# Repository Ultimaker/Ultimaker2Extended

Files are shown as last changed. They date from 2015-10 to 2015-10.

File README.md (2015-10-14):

# Ultimaker2Extended
Bill of Materials and parts for Ultimaker2Extended

In this repository you will find the documentation and source files for all parts in the Ultimaker2 Extended 3D printer. In the Bill Of Materials (BOM) repository all the parts are numbered and named with the correct amounts. Every part has a separate directory containing all the relevant files. The 9407 is a subsytem. The parts can also be found in the separate directories.

The electronic files can be found in the directory 1155 Print Table Heated Bed; 1249 Ulticontroller board and 1546 Ultimainboard V2.1.4.

If you are missing a part or information feel free to file an issue on github.

Harma Woldhuis <br>
Ultimaker Research and Development

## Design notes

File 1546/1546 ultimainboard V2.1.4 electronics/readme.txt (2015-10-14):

The UltiMainboard 2.x.x electronics are released under GPLv2 license.
And are based on the origonal Ultimaker electronics design by Jan-Jaap Schuurman, Siert Wijnia and ErikDeBruijn at http://reprap.org/wiki/Ultimaker's_v1.5.7_PCB
As well as the ArduinoMega2560 by Arduino: http://arduino.cc/en/Main/arduinoBoardMega2560

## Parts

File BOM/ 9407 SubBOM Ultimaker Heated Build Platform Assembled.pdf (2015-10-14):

## SubBOM

Total quantity parts | 40
Partnummer | Naam | Quantity
1152 B | Table Spring D2150 | 3
1153 B | Print Table Base Plate | 1
1155 C | Print Table Heated Bed | 1
1170 B | Square Flanged Linear Bearing LMK12LUU | 2
1183 C | Heated Bed Cable | 1
1187 A | Trapezoidal Lead Nut | 1
1202 B | ISO 7380 M3x10 | 6
1206 B | ISO 7380 M3x20 | 1
1217 A | ISO 7380 M4x10 A2 | 8
1243 B | Heated Bed Cable Clip | 1
1256 A | Build Platform Glass Retainer Back | 2
1257 B | Knurled Nut Platform | 3
1288 A | Washer M6 | 3
1355 B | Heated Bed Bolt 8 mm | 4
1356 B | Heated Bed Bolt 20 mm | 3

## 9407 Ultimaker Heated Build Platform Assembled

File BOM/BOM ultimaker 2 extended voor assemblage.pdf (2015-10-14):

9068-A | Ultimaker 2 Extended voor assemblage

per 30-12-2014
Total quantity parts | 318
Partnummer | | Name | Quantity
1011 | B | Y-linear shaft | 2
1012 | B | X-linear shaft | 2
1021 | A | Ball Bearing 688-2RS | 1
1024 | D | Limit Switch, Black Short Wire | 1
1056 | A | Sintered Bushing | 4
1065 | B | Linear Bearing LM6LUU | 2
1069 | A | Tube Coupling Collet | 2
1071 | A | Clamp Clip | 2
1140 | A | Feeder Spring DR2110 | 1
1156 | A | Z-shaft Cap Bottom | 2
1165 | A | Timing Pulley 5mm Shaft GT2 | 2
1166 | C | Timing Pulley 8mm Shaft GT2 | 8
1167 | D | Timing Pulley Double 8mm Shaft GT2 | 1
1168 | B | Sliding Block Spring | 4
1171 | B | Double flat Cable 10 Wire | 1
1172 | A | Print Head Shaft X | 1
1173 | A | Print Head Shaft Y | 1
1176 | A | Spacer 8.2x10x5 | 2
1177 | A | Spacer 8.2x10x10 | 4
1178 | A | Spacer 8.2x10x25 | 1
1179 | D | Feeder Motor | 1
1186 | E | Print Head Cable | 1
1188 | A | Timing Belt GT2 200 | 2
1189 | A | Timing Belt GT2 610 | 4
| | nuts and bolts
1200 | A | ISO 7380 M3x8 | 8
1201 | C | Washer Large M3 | 12
1202 | B | ISO 7380 M3x10 | 7
1203 | B | ISO 7380 M3x12 | 11
1204 | B | ISO 7380 M3x16 | 44
1206 | B | ISO 7380 M3x20 | 1
1207 | B | ISO 7380 M3x25 | 16
1209 | C | Nut M3 | 1
1211 | A | Set Screw M4x4 | 11
1212 | B | Set Screw M3x3 | 1
1213 | B | DIN 562 Square Nut M3 A2 | 40
1214 | A | ISO 7040 Nut M3 Prev. torque A2 | 12
1220 | A | Ball Bearing F688-2RS | 8
1234 | E | Bottom Panel UM2 | 1
1235 | D | Top Panel UM2 | 1
1240 | C | Main Board Electronics Cover | 1
1241 | B | Motor Spacer UM2 | 2

1242 | A | Spacer 3.2 x 6x 10 | 4
1244 | A | Knob Front UM2 | 1
1245 | A | Knob Housing UM2 | 1
1247 | A | Display Oled Blue | 1
1249 | A | Ulticontroller Board | 1
1250 | B | SD card 4G | 1
1251 | B | Ulticontroller Electronics Cover | 1
1255 | A | Sliding Block Half UM2 | 8
1258 | G | Feeder Part A | 1
1259 | G | Feeder Part B | 1
1264 | D | Feeder Nut Holder | 1
1266 | C | Bowden tube | 1
1268 | B | Heater Cartridge 24V 25W | 1
1279 | A | Feeder Ring | 1
1281 | C | Braided Sleeve Clip | 5
1287 | A | Washer M7 | 1
1301 | D

Integrated nozzle heater block
3mm filament | 1
1306 | C | Hot end holder bottom | 1
1307 | C | Hot end holder top | 1
1308 | C | Cooling Rib Hot End | 1
1310 | B | Hot end Isolator | 1
1311 | A | Spring D2000 | 1
1313 | A | Model Cooling Fan 12VDC 0.1 A | 2
1315 | A | Jumper | 2
1321 | C | Print Head Middle | 1
1322 | D | Print Head Bottom | 1
1330 | B | Hot-end Cooling Fan 5VDC 0.08A | 1
1348 | A | ISO 7380 M3x4 A2 | 4
1351 | A | ISO 4762 M2,5x10 | 2
1354 | A | ISO 724 Hex nut M7 | 1
1357 | A | DIN 913 M3x14 | 1
1358 | A | chipboard panel screw 2.5x16 | 8
1363 | A | Ferrite Core | 2
1364 | A | PTFE Isolator Coupler Glass Filled 3.2 mm | 1
1365 | A | Dual Fan Bracket Safety | 1
1366 | A | PTFE nozzle ring | 1
1521 | A | Short Print Head Thumb Screw | 4
1546 | A | Ultimainboard V2.1.4 | 1
1748 | D | Print head top single hole | 1
1814 | | feeder knurled wheel long | 1

1816 | feeder idler lever part A | 1
1817 | feeder idler lever part B | 1
2201 | E | Z-linear shaft | 2
2202 | A | Z-Motor with Trapezoidal Lead Screw | 1
2203 | B | X,Y motor | 2
2204 | B | Limit Switch, Blue Wire | 1
2205 | B | Limit Switch, Red Wire | 1
2206 | A | LED Strip Cold white | 1
2211 | B | Back Panel | 1
2212 | A | Left Panel | 1
2213 | A | Right Panel | 1
2214 | A | Front Panel | 1
2215 | A | Print Table Back Cover | 1
2222 | A | Cable Cover | 2
2225 | C | PT100B sensor | 1

9407

subBOM Ultimaker Heated Build
Platform Assembled | 1

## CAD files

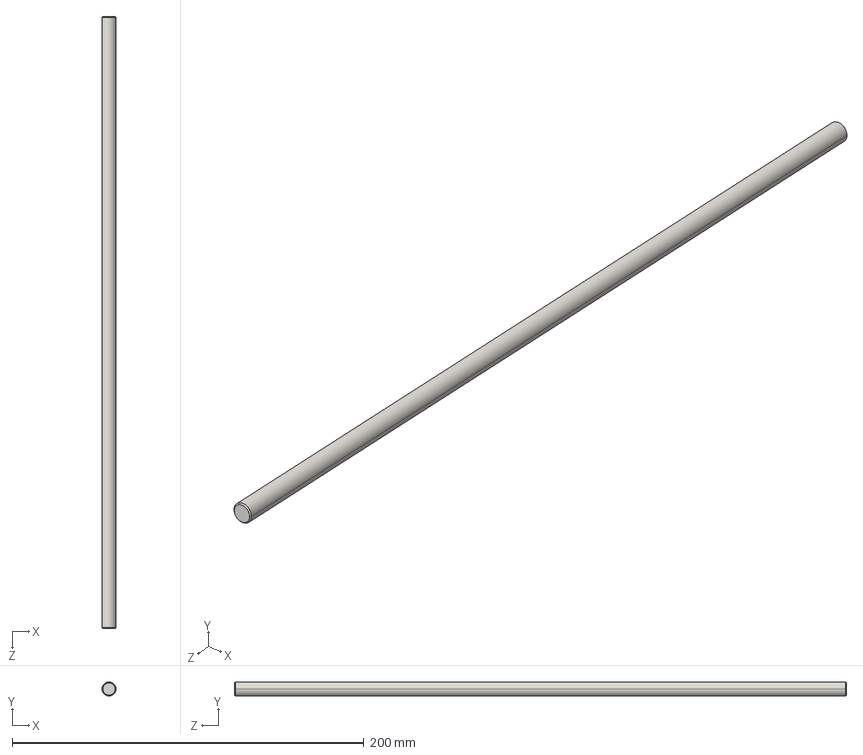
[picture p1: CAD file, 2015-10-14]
1011/1011-B.STEP
8.00 x 8.00 x 348.0 mm

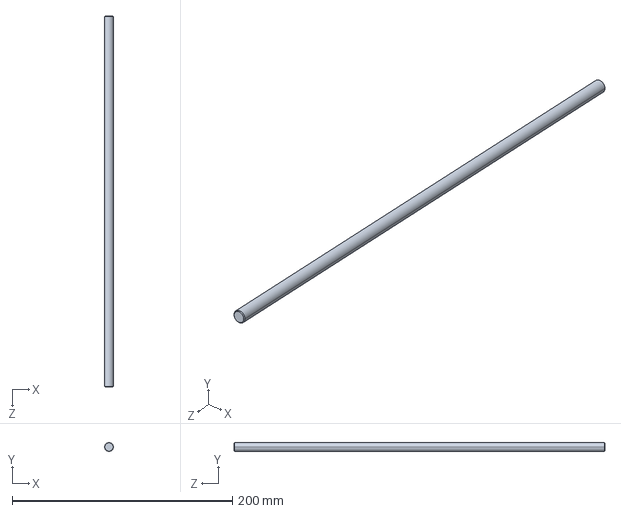
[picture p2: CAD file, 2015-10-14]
1012/1012-B.STEP
8.00 x 8.00 x 337.0 mm

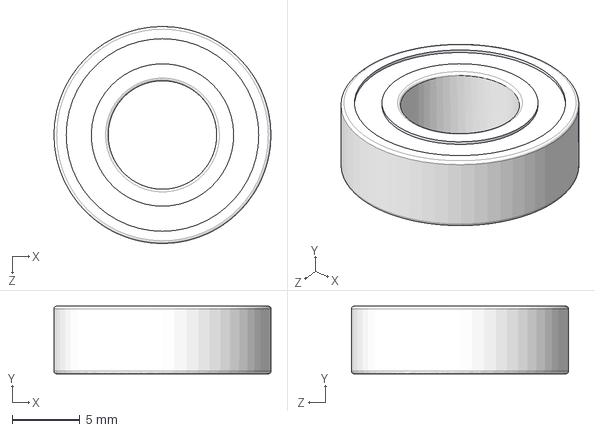
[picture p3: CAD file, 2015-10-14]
1021/1021-Z1P-A.STEP
16.0 x 5.00 x 16.0 mm

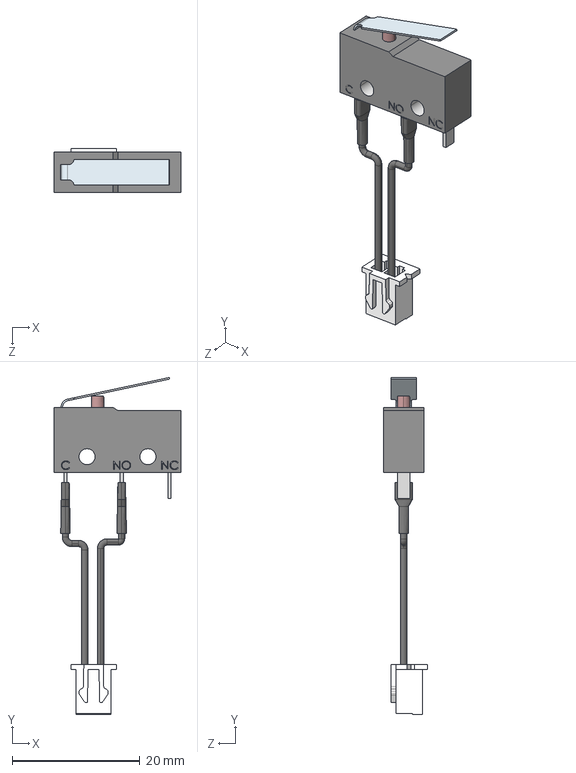
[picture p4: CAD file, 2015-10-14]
1024/1024-D.STEP
19.8 x 52.7 x 6.90 mm

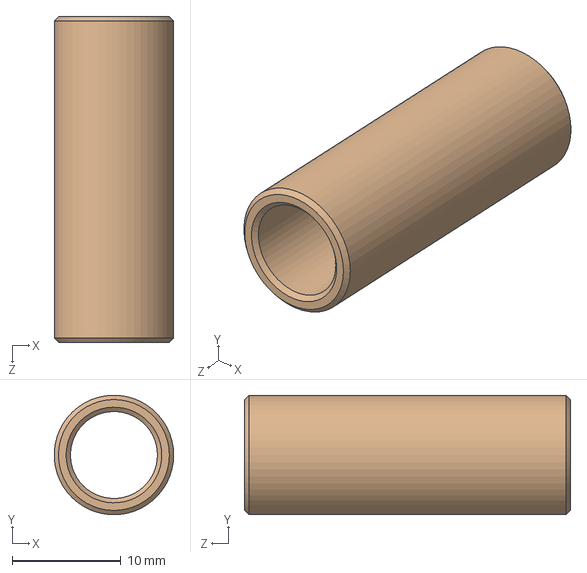
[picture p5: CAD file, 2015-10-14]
1056/1056-A2P-A.STEP
11.0 x 11.0 x 30.0 mm

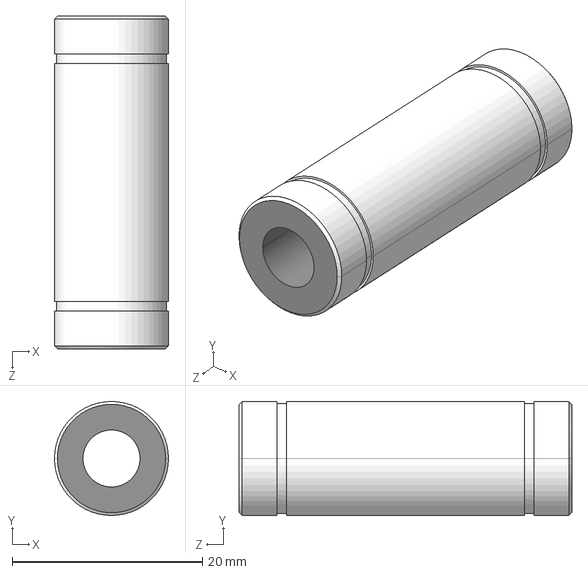
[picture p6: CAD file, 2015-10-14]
1065/1065-Z1P-B.STEP
12.0 x 12.0 x 35.0 mm

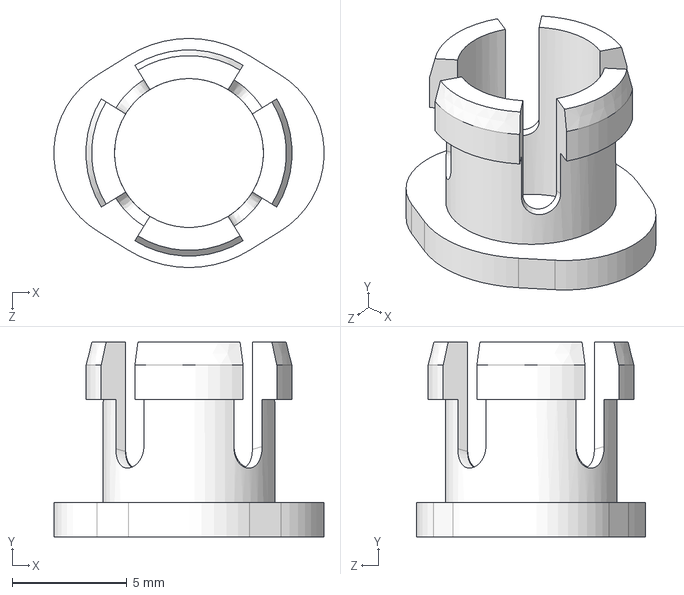
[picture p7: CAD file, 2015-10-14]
1069/1069-Z1P-A.STEP
11.8 x 8.50 x 10.00 mm

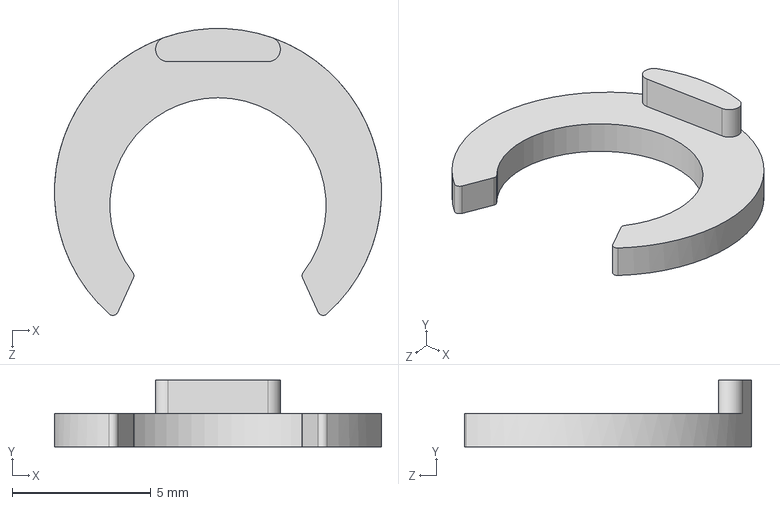
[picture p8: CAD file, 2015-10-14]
1071/1071-Z1P-A.STEP
11.8 x 2.40 x 10.3 mm

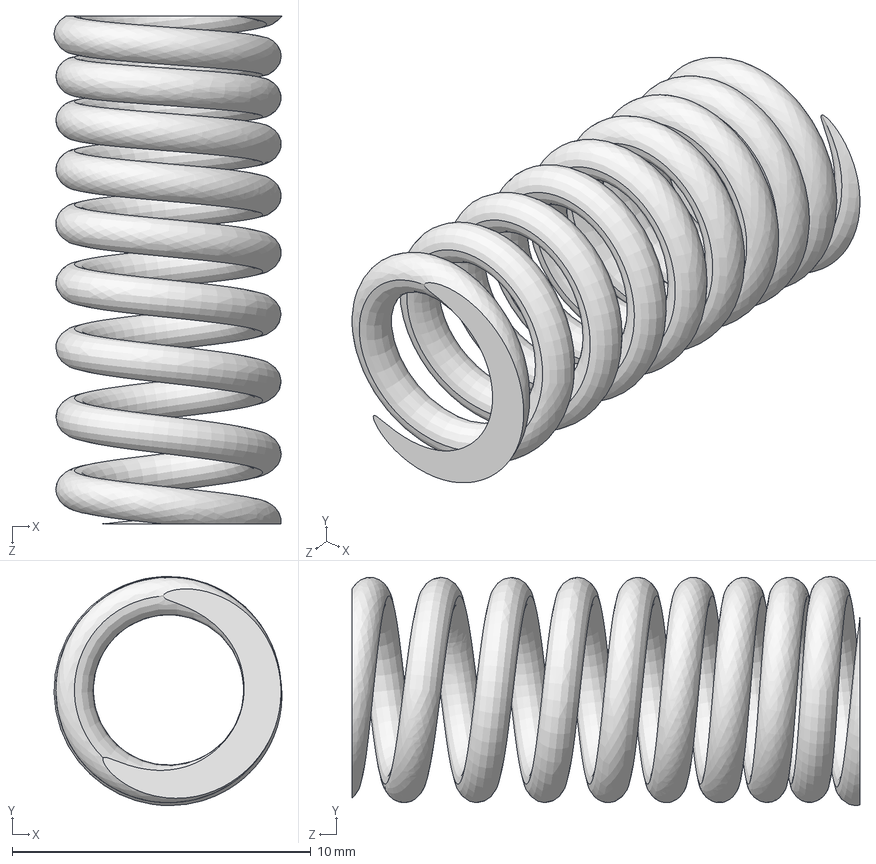
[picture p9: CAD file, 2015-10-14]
1140/1140-01.STEP
7.63 x 7.67 x 17.0 mm

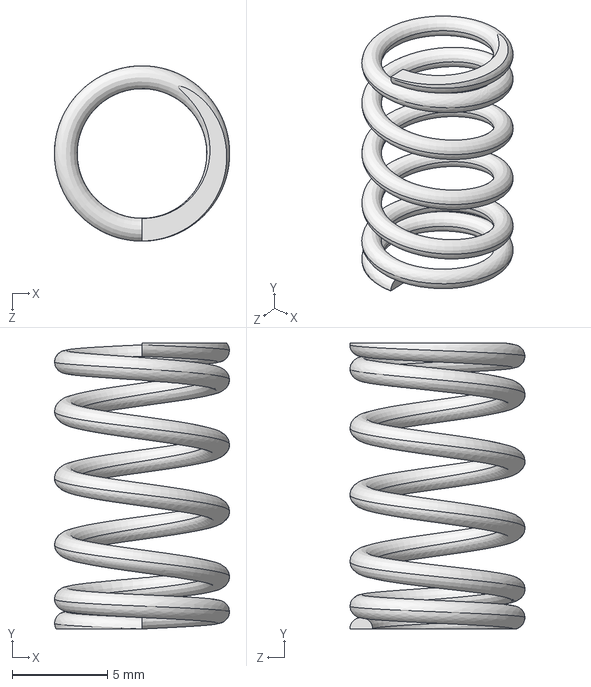
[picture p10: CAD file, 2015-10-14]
1152/1152-B2P-B.STEP
9.20 x 15.0 x 9.20 mm

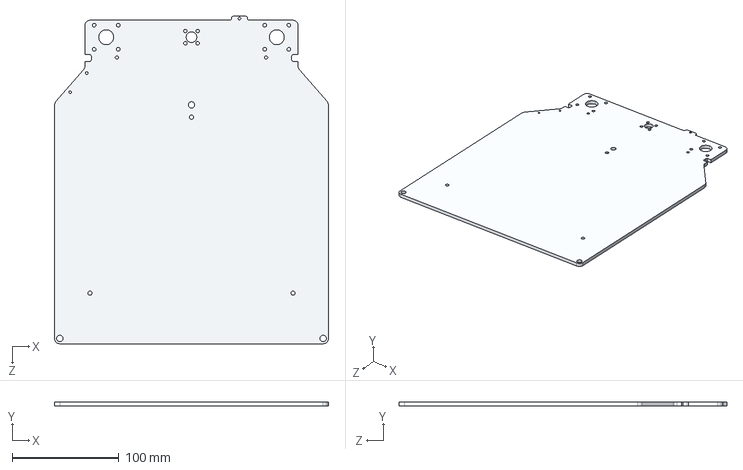
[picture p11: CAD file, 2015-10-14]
1153/1153-B2P-B.STEP
257.0 x 4.00 x 307.2 mm

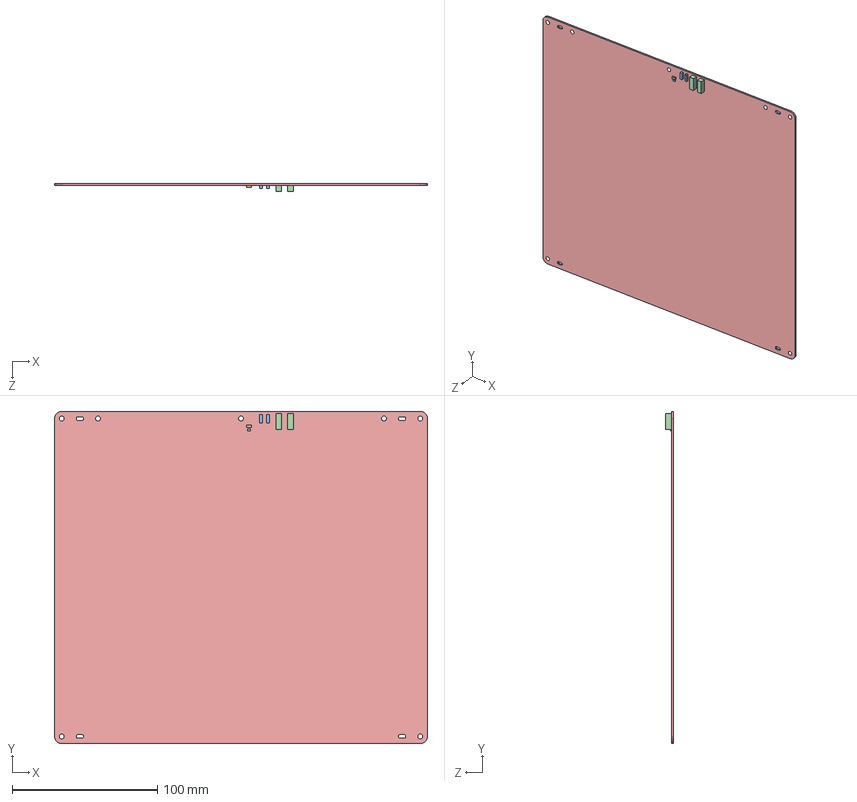
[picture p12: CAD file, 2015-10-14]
1155/1155-C.STEP
257.0 x 229.0 x 5.50 mm

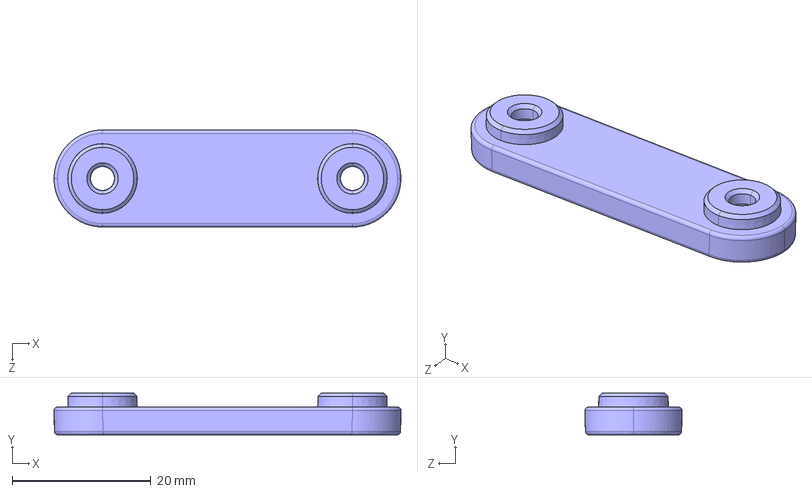
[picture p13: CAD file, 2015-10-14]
1156/1156-B2P-A.STEP
50.0 x 6.00 x 14.0 mm

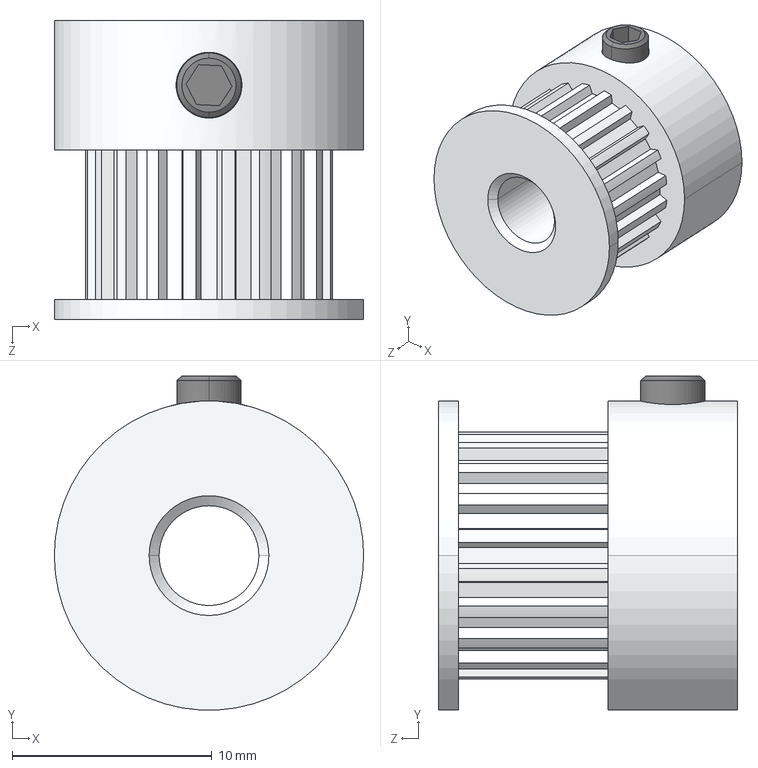
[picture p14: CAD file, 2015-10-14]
1165/1165-B2P-A.STEP
15.5 x 16.7 x 15.0 mm

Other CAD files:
1166/1166-C.STEP
1167/1167-D.STEP
1168/1168-B2P-B.STEP
1170/1170-B2P-B.STEP
1172/1172-B2P-A.STEP
1173/1173-B2P-A.STEP
1176/1176-B1P-A.STEP
1177/1177-B1P-A.STEP
1178/1178-B1P-A.STEP
1179/1179-D.STEP
1187/1187-B2P-A.STEP
1188/1188-B2P-A.STEP
1189/1189-B2P-A.STEP
1200/1200-Z1P-A ISO 7380 M3x8 new.STEP
1201/1201-Z1P-C.STEP
1202/1202-Z1P-B.STEP
1203/1203-Z1P-B.STEP
1204/1204-Z1P-B.STEP
1206/1206-Z1P-B.STEP
1207/1207-Z1P-B.STEP
1209/1209-C.STEP
1211/1211-Z1P-A.STEP
1212/1212-Z1P-B.STEP
1213/1213-Z1P-B.STEP
1214/1214-Z1P-A.STEP
1217/1217-A.STEP
1220/1220-A.STEP
1234/1234-B2P-E Buitenkant.DXF
1235/1235-B2P-D Buitenkant.DXF
1235/1235-B2P-D.STEP
1240/1240-C.DXF
1240/1240-C.STEP
1241/1241-B2P-B.STEP
1242/1242-B2P-A.STEP
1243/1243-B2P-B.STEP
1244/1244-B2P-A.STEP
1245/1245-B2P-A.STEP
1247/1247-B2P-A.STEP
1250/1250-B.STEP
1251/1251-B.DXF
1255/1255-B2P-A.STEP
1256/1256-B2P-A.STEP
1257/1257-B2P-B.STEP
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

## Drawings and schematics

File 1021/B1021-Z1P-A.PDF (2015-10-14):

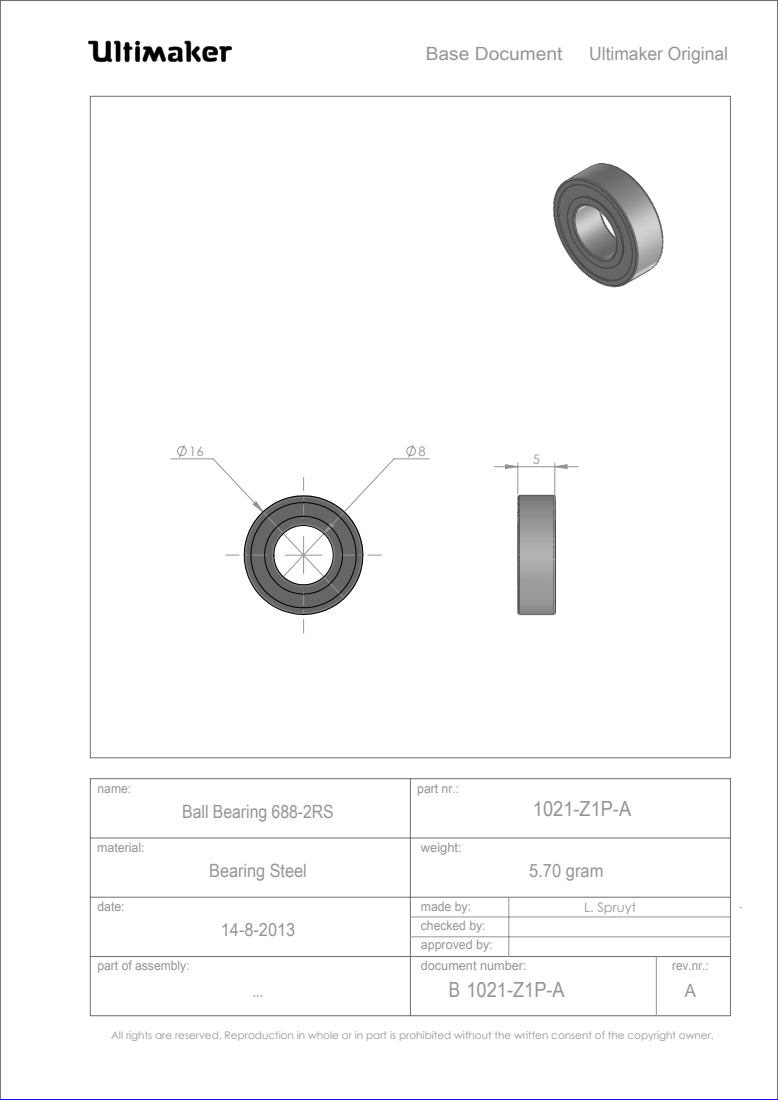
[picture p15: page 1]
Bearing Steel; 5.70 gram; Ball Bearing 688-2RS; Ultimaker Original; part of assembly:; rev.nr.:; part nr.:; made by:; Base Document; approved by:; checked by:; L. Spruyt; document number: B 1021-Z1P-A

All rights are reserved. Reproduction in whole or in part is prohibited without the written consent of the copyright owner.

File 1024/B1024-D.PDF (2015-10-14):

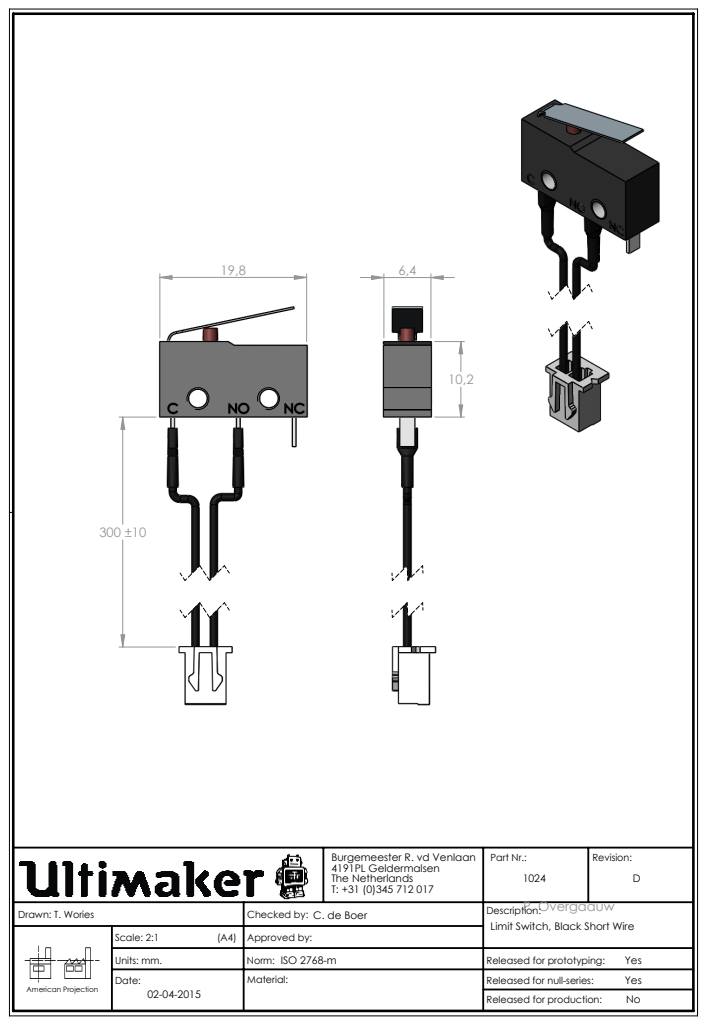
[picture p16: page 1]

Burgemeester R. vd Venlaan 4191PL Geldermalsen The Netherlands T: +31 (0)345 712 017 | Part Nr.: 1024 | Revision: D

Drawn: T. Wories | Checked by: C. de Boer | P. Overgaauw Description: Limit Switch, Black Short Wire

American Projection | Scale: 2:1 (A4) | Approved by:

Units: mm. | Norm: ISO 2768-m | Released for prototyping: Yes
Date: 02-04-2015 | Material: | Released for null-series: Yes

Released for production:

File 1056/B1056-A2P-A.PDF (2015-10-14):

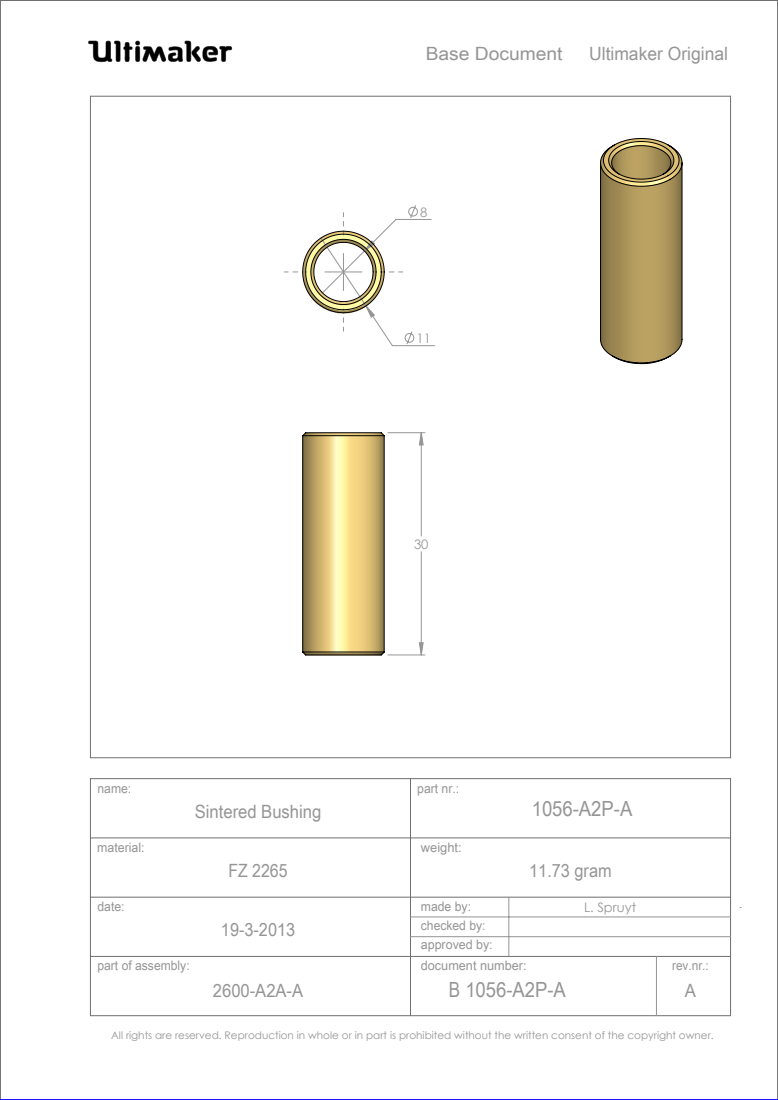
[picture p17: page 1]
11.73 gram; Sintered Bushing; Ultimaker Original; part of assembly:; rev.nr.:; part nr.:; made by:; Base Document; approved by:; checked by:; L. Spruyt; document number: B 1056-A2P-A

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

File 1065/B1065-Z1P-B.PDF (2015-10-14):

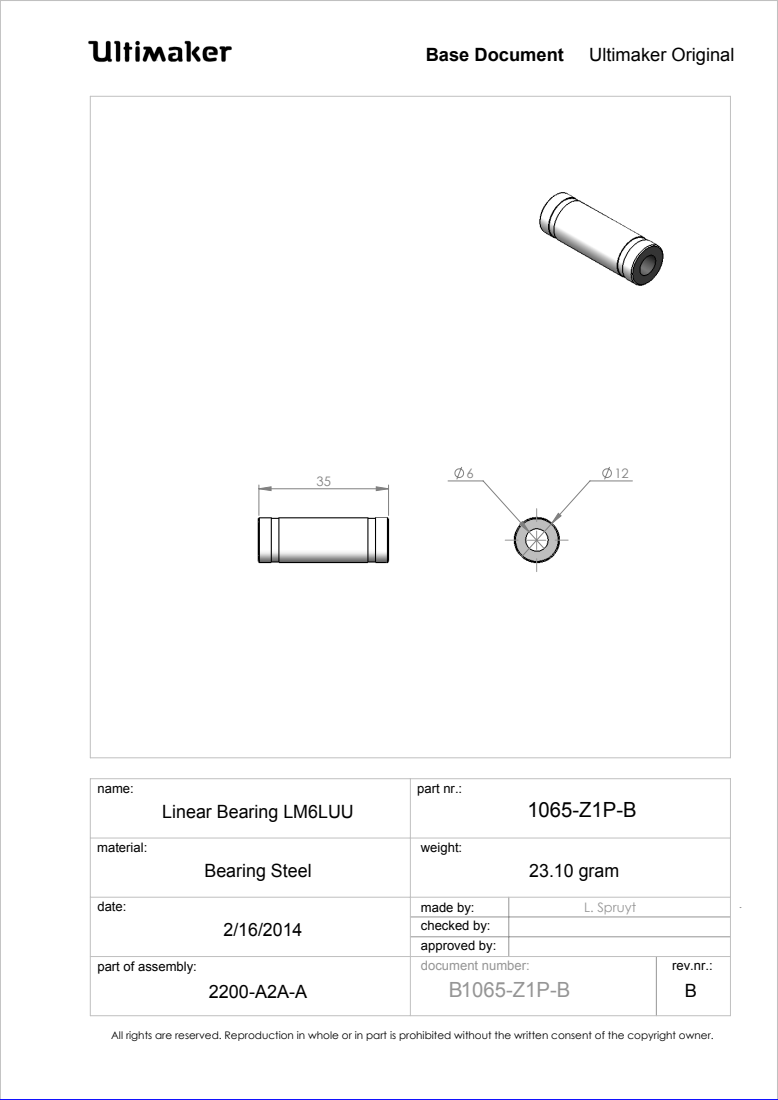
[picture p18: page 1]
Bearing Steel; 23.10 gram; Linear Bearing LM6LUU; Ultimaker Original; part of assembly:; rev.nr.:; part nr.:; made by:; Base Document; approved by:; checked by:; L. Spruyt; document number:

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

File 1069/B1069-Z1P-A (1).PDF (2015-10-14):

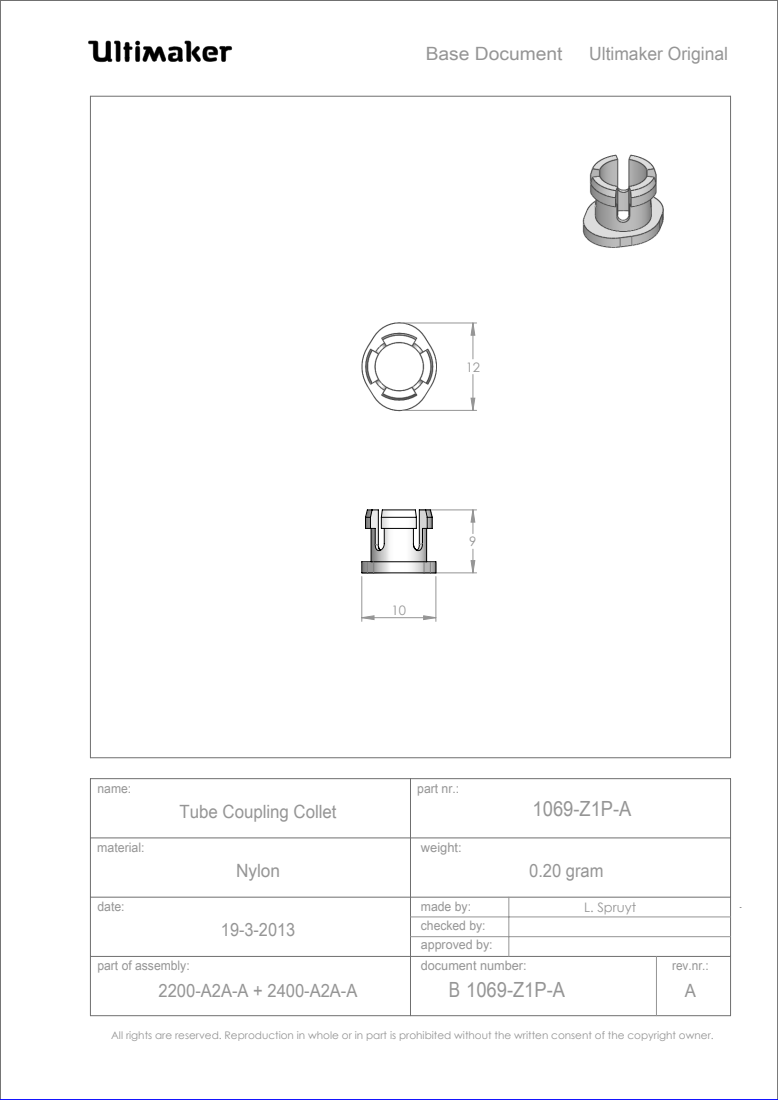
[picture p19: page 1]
Nylon; 0.20 gram; Ultimaker Original; part of assembly:; rev.nr.:; part nr.:; made by:; Base Document; approved by:; checked by:; L. Spruyt; document number: B 1069-Z1P-A

Tube Coupling Collet

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

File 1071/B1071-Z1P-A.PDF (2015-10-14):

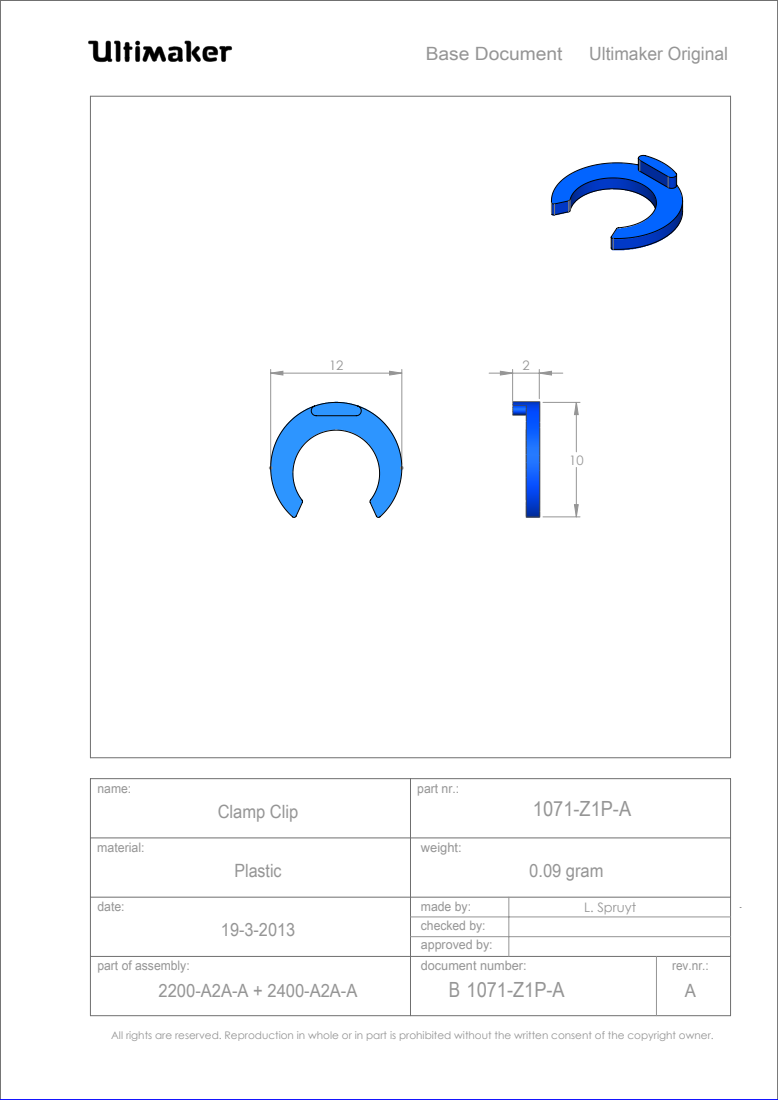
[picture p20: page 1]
Plastic; 0.09 gram; Clamp Clip; Ultimaker Original; part of assembly:; rev.nr.:; part nr.:; made by:; Base Document; approved by:; checked by:; L. Spruyt; document number: B 1071-Z1P-A

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

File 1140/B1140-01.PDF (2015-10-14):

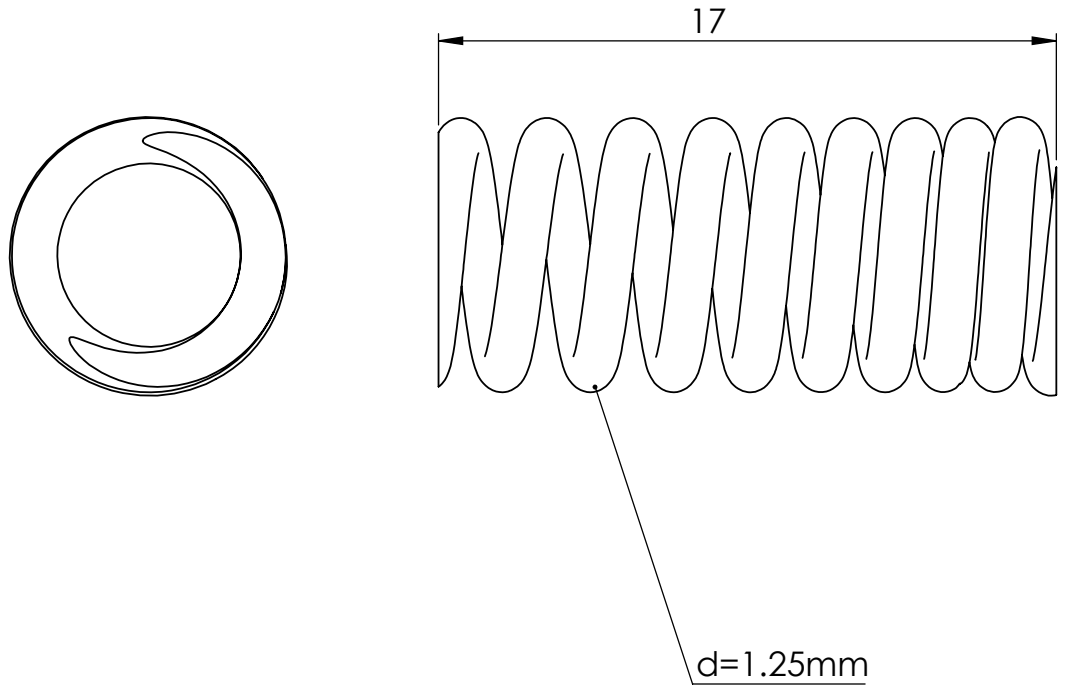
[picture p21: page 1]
Part Nr.: 1143-01; Product: Ultimaker 2

Burgemeester R. vd Venlaan
4191PL Geldermalsen
The Netherlands

Drawn: Ivar Kraaijevanger | Checked by: **** | Description: Feeder Spring DR2110

American Projection | Scale: 5:1 (A4) | Approved by: ****

Units: mm. | Material: Stainless Steel, DIN 17.224 | Released for prototyping: Yes
Date: 24-11-2014 | Norm: DIN 2095-2 | Released for null-series: Yes
Sheet number: 2 of 2 | Amount: 1 | Released for production: Yes

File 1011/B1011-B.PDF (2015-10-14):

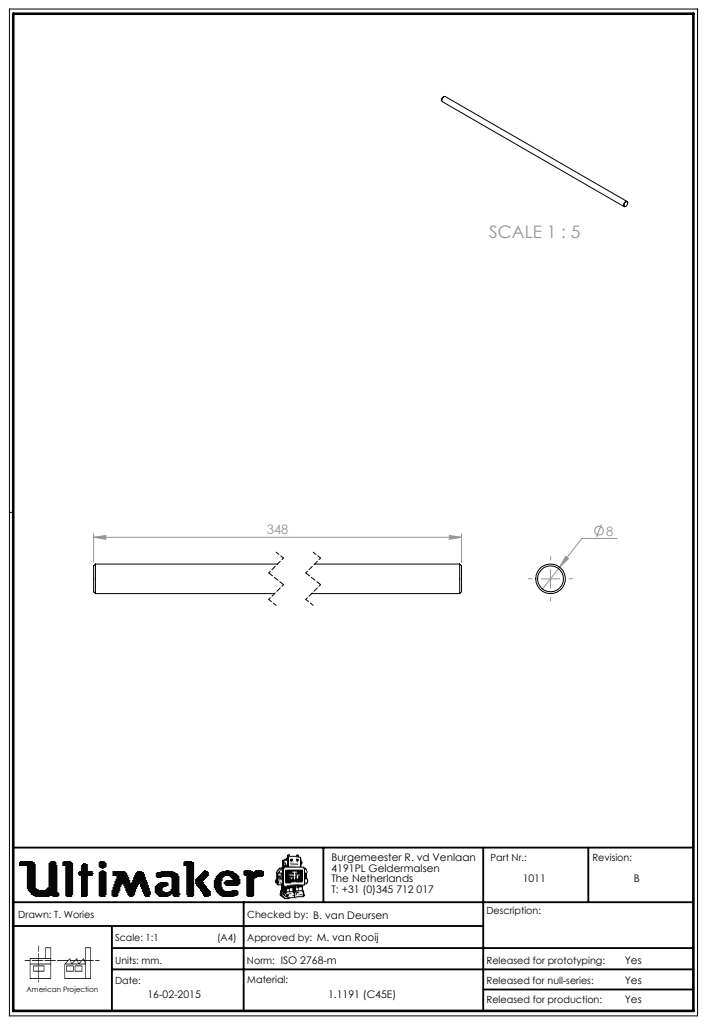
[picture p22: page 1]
SCALE 1 : 5

Burgemeester R. vd Venlaan 4191PL Geldermalsen The Netherlands T: +31 (0)345 712 017 | Part Nr.: 1011 | Revision: B

Drawn: T. Wories | Checked by: B. van Deursen | Description:

American Projection | Scale: 1:1 (A4) | Approved by: M. van Rooij

Units: mm. | Norm: ISO 2768-m | Released for prototyping: Yes
Date: 16-02-2015 | Material: 1.1191 (C45E) | Released for null-series: Yes

Released for production:

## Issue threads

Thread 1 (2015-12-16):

missing LMK12LUU in BOM

justgook, 2015-12-16:
missing LMK12LUU in BOM

harmawoldhuis, 2015-12-16:
In BOM directory: 9407 subBOM Ultimaker Heated Build Platform Assembled the 1170 LMK12 LUU can be found

Closed 2015-12-16.
